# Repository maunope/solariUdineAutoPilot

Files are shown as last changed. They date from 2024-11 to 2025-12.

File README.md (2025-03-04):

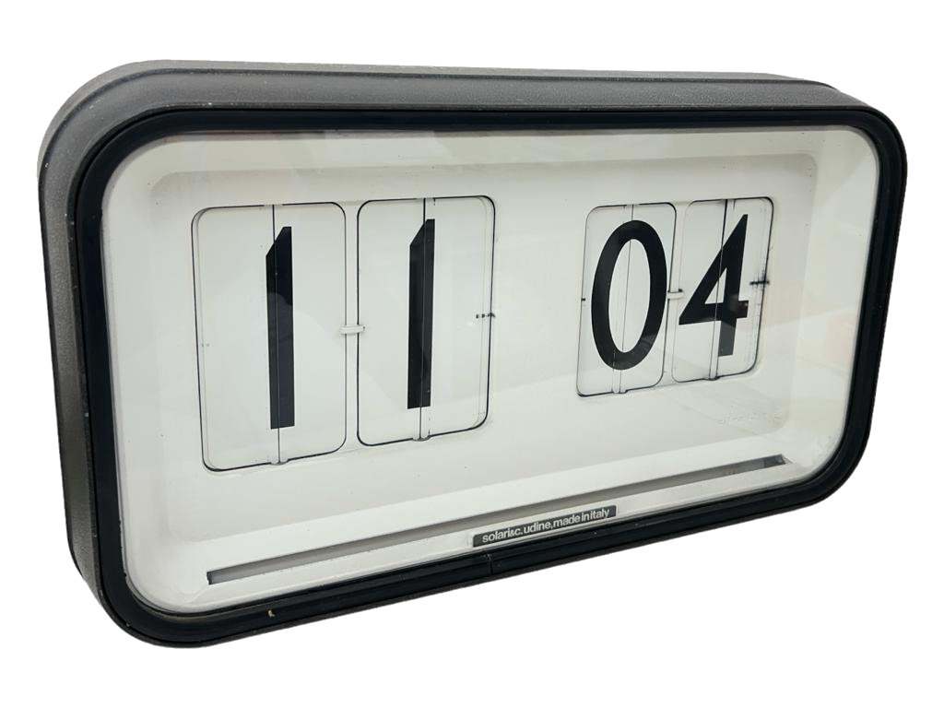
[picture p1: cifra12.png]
Solari Udine Cifra 12


# Disclaimer
This is still a prototype, the circuit design was built and tested on a perfboard, the kicad board design was never tested.  use at your risk and plz **don't  come whining if you damage your flip clock or set your house on fire.**

# Solari Udine Auto Pilot

Arduino based Solari Udine Clock controller, suitable for alternating pulse Solari Udine Clock motors (i.e. Cifra 12). Controls hours and minutes, no calendar functions are provided. The current board design accepts a single Vcc in, either 12V or 24V, from an external power source. 

**Main features:**   
- Self adjusts after a power loss
- Handles DST (Central Europe rules)
- Allows manual adjustment

A led provides visual feedback, an optional LCD1602 can be plugged in to display status.

The software tries to mitigate strain on the flip clock limiting the number and frequency of rollers turns:
- Turns are limited to 1 every 3 seconds (manual step adjustment bypasses this)
- If the clock is more than 120 minutes behind, movement is paused till the next day (a halted clock displays the right time once a day after all **:-)**)
- If the eeprom or rtc module fail, no pulses are sent to the motor
- If the rtc module crashes, attempts are made to restore the last known consistent timestamp
- A hardware circuit limits pulse duration and frequency to 1 second.
- the circuit board has hardware protection avoiding prolonged motor pulses, set to 1 second. Once a pulse is sent, following ones are delayed until the hw protection has completed its cycle. Note that it is totally possible to build the board without the 555 timer, just hardwire L293D enable pins to high, software will work just fine.

The following features improve durability and operation:
- The system self restart once per week
- Eeprom writes are spread over a 256kbit eeprom, this should guarantee at least 20 years of operation before writes start to fail, more likely 50-70
- If eeprom stored time is unavailable, the clock halts until it is adjusted
- If RTC module is unavailable, the clock blinks for 30 seconds and then resets
- The Arduino will stay powered down approx 95% of the time during regular operation, saving considerable power. As a side effect, minutes will flip within +/- 2 seconds of when RTC time ticks a minute.  

## Dependencies

- [LiquidCrustal I2C](https://github.com/johnrickman/LiquidCrystal_I2C)
- [RTClib](https://github.com/adafruit/RTClib)
- [Regexp](https://github.com/nickgammon/Regexp)
- [SparkFun External EEPROM Arduino Library](https://github.com/sparkfun/SparkFun_External_EEPROM_Arduino_Library)
- [Rocket Scream Low Power](https://github.com/rocketscream/Low-Power)

## Circuit Board

**WORK IN PROGRESS** check the schematic in this repo, I've built and tested it on perfboard, board design might not be 100% correct, and definitely the layout could 
use some improvement.

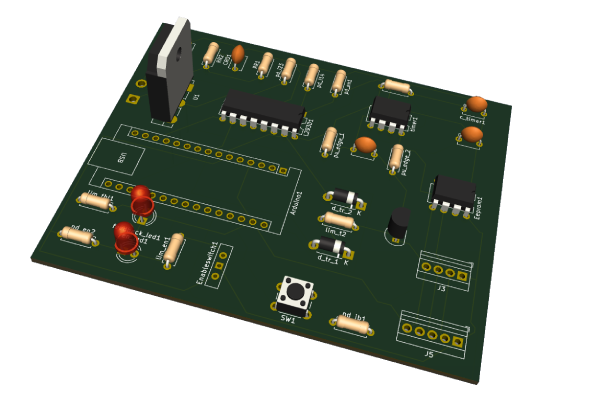
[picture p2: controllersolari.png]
Solari Udine Autopilot Circuit Board


**"Simplified"** board version uses some 30% less components removing the following features:

- Hardware limitation of pulses duration
- Paralleled L293D outputs

Considering how unlikely it is for the sketch to remain stuck with motor output set high, you might want to save yourself some hassle, expecially if you're building on perfboard.

I've built the board using these cheap DS3231 bought off Amazon, the design uses a male connector matching their Vcc-signal-signal-NC-Ground pinout, you might want to use something different and change the board design accordingly.
One good thing about these is they're small enough and can be easily swapped for testing and debugging

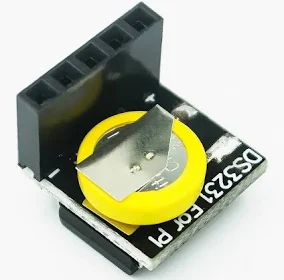
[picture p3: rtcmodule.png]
RTC Module


**How to read led signals**

Either for good or bad news, green led will flash. red will stay on when general enable switch is on

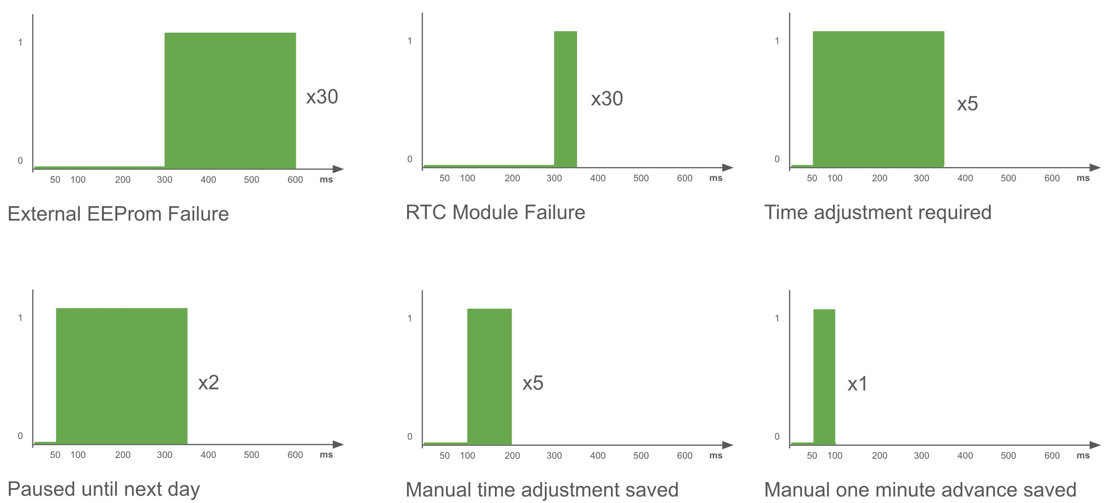
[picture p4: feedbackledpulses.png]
Feedback led pulses interpretation card


## How to install and adjust

**First things first, let's not fry stuff**
- If you built the board yourself, either run the Arduino sketch with  SET_COMPILE_TIME_TO_RTC flag turned on or use serial commands to prime the RTC module.
- Check your clock coil working voltage. Most accept 24V plus 12V or 48V with different wiring. **The current board design was tested with a 12 V external power source, 24V should work fine albeit with the tension regulator running hotter, 48V is beyond the regulator specs**
- Check your coil max current draw, one L293D with paralleled channels can drive up to 1200mA, no Solari Udine clock should draw more than that
- Unplug the clock, wire your power supply and the clock motor coil
- Turn the enable switch *OFF*
- Power the board.
 **No smoke? good.**
- On the first start, a manual time adjust is required,  "Time Adjustment Required" pattern will flash on the feedback led
- Manually adjust the clock flip rolls to match current time, the optional LCD display displays it on the first line
- Dial at least one minute advance with the button, this will prime pulse direction
- When the clock time matches RTC time, *Press the push button for 3 seconds until "Manual Time Adjustment Saved" pattern flashes*
- Turn the enable switch *ON*

The controller will now keep the flip clock display aligned with the internal RTC clock.

## Enabling motor movement

A switch allows to pause motor movement for maintenance and dialing in commands, the clock will catch up automatically once enable is resumed.
A led will remain **ON** while movement is paused.
the switch also disables deep sleep time and prepares the Arduino for accepting commands: wait until feedback led blinks once after pausing movement, then dial button or serial commands.

## Push buttons commands

*Important* only dial pushbutton commands with the motor enable switch turned off 

- Brief press: advances the clock 1 minute, led blinks briefly
- Three seconds press: aligns eeprom time with RTC time, for manual adjustment, led blinks on a pattern 

## Serial port commands

*Important* only dial serial commands with the motor enable switch turned off 

Commands format: **(<<|>>)[A-Z]{1,10}[a-z,A-Z,0-9]{1,20}**

- **<<** to read info, **>>** to set
- command name, in caps
- (where applicable) parameter

One command per line, max 32 chars long. the parser is pretty crude, pls stick to tested commands ;-) 

**Available commands**:

- **<<BOOTTIMESTAMP** prints the curent boot timestamp
- **>>COMPILEDATETIME** align RTC date and time to the sketch compilation timestamp
- **<<COMPILEDATETIME** print the sketch build timestamp
- **>>DAILYSECODNSOFFSET[+-][0-9]{3}$** (i.e: >>DAILYSECODNSOFFSET+010, DAILYSECODNSOFFSET+000, DAILYSECODNSOFFSET-020) stores the desided number of daily RTC error compensation to eeprom.
- **<<DAILYSECODNSOFFSET** print daily seconds of  RTC error correction setting stored in the eeprom
- **>>RTCDATETIMEyyymmddhhmmss** (i.e: >>DATETTIME20241119235959) set RTC date and time, takes standard time, *not DST*.
- **<<RTCDATETIME** print RTC date and time
- **<<EEPROMDATA** print eeprom date, time and clock status information

## Build flags

-DEBUG_MODE enable serial port and LCD debug messages, disbales sleep time  and force reinitialization of eeprom and rtc module on each read
-SET_COMPILE_TIME_TO_RTC forces writing sketch build time to RTC on each boot, only use to program new rtc modules.

## Troubleshooting
**Q:** Instead of catching up the clock is standing still and the "Paused until next day" pattern flashes:

**A:** When more than 120 minutes are to be catched up, automatic adjustment will pause and wait for clock time to be right again the next day.

**Q:** The Arduino keeps resetting every half a minute or so, the feedback led flashes

**A:**  Either the eeprom or RTC clock aren't responding, the board needs fixing

**Q:**  I've hooked up a display, now what?

**A:** Note that the display only works when DEBUG_MODE flag is raised

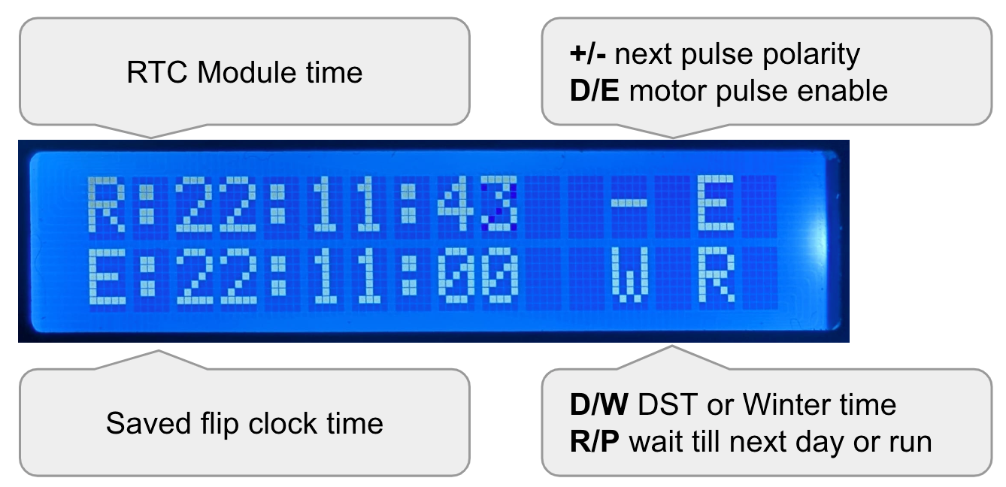
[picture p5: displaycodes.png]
Optional display fields


**Q:**  How can I tell if my eeprom is corrupted or simply requires initialization?

**A:**  "Adj. time" on the display or "No valid time set in eeprom, please adjust clock" on the Serial are good news.

**Q:** My RTC module lost its time configuration!

**A:** >>DATETIME[0-9]+ command should fix it, however, if it happens again, the module batttery might be drained

**Q:** I can't tell what's going on with eeprom data

**A:** <<EEPROMDATA command can extracts all the info saved on the eeprom

**Q:** LCD doesn't display anyting, and/or serial messages are missing

**A:** set DEBUG_MODE build flag and upload firmware again

**Q:** **(serial|button) commands** are not working!

**A:** they only work reliably when motor movement is paused (solid red led), during regular operation the Arduino is awake and responding to commands for only few seconds per minute, good luck catching it awake! :-) 

**Q:** My clock drifts X seconds ahead/behind everyday

**A:** Buy a proper RTC module next time! :-) there's a handy feature to correct this, if the drift is the same every day, see serial commands

**Q:** My clock drifts X *minutes* ahead/behind everyday

**A:** Hikes! that's not OK! try a different RTC module, then check your board for errors on I2C bus pullup resistors and +5v power. I've tested the board design powering I2C devices straight from a tension regulator bypassing the Arduino's internal one, either do the same or dig  sleep configurations to figure how to keep the RTC powered during sleep. In case you figure something out, open a PR here :-)

**Q:** I got a RTC failure message/blink and then the board rebooted

**A:** Your RTC went nuts! it happens every now and then with cheap *ss modules, mine's MBTF is around 4 months, the sketch tries its best to recover to the last timestamp that made sense if it detects the RTC is acting up

**Q:** No matter what I do, the clock keeps flipping!

**A:** The RTC module is returning wrong timestamps, and the checks I've put in place are not working. :-( 
    compile the sketch in debug mode, use serial commands to check what timestamp is recorded in the RTC module and fix it, 
    realing eeprom time with RTC time, reboot, and check after a few minutes that the RTC module is behaving. If you wish, drop me an email about the problem including the timestamp you had in the RTC module and then one in you EEPROM (or, even better, figure what's wrong and open a PR :-) )

**Q:** That PCB design is **lame**!

**A:** It is. any help much appreciated! ;-)

## Todo
- when disabling motion while sleep is skipped (i.e. 2 secs after a pulse), feedback led doens't blink
- Add support for bluetooth communication
- Improve kicad design
- Figure some predictable behavior for when RTC is known to be f*cked up, i.e start from 1970 and stop calculating dst
- Finish String calss removal
- Remove dependency from regexp library

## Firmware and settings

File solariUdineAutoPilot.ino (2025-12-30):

//#define DEBUG_MODE

#ifdef DEBUG_MODE
#include <LiquidCrystal_I2C.h>         //https://github.com/johnrickman/LiquidCrystal_I2C
#endif

#include <LowPower.h>                  //https://github.com/rocketscream/Low-Power
#include <RTClib.h>                    //https://github.com/adafruit/RTClib
#include <SparkFun_External_EEPROM.h>  //https://github.com/sparkfun/SparkFun_External_EEPROM_Arduino_Library



//never leave this flag on on regular operation, it pretty much defeats the purpose of using this board
//#define SET_COMPILE_TIME_TO_RTC

//struct for the EEProm index page
struct EepromIndexDescriptor {
  unsigned long signature;
  int pageOffset = 0;
  int dailySecondsOffset = 0;
};

// struct for clock status to be saved to the eeprom
struct EepromData {
  //initializing at WINT_MAX ensures that if the conrtoller is run without further initialization
  //it won't send pulses
  DateTime dateTime = DateTime(WINT_MAX);
  int nextPulsePolarity = 0;
  int currentWrites = 0;
  bool pausedTillNextDay = false;
};


//debug mode redirects stdout to the serial port, this avoids the need for strings buffering
#ifdef DEBUG_MODE
// Define a custom putchar function to redirect output to Serial
int putCharToSerial(char c, FILE *stream) {
  if (stream == stdout) { // Check if it's standard output
    Serial.write(c);
  }
  return 0;
}

// Declare a FILE stream for stdout (no initializer here!)
FILE customStdOut;
//printf macro, together with putCharToSerial driver debug messages straight to the Serial port,
//stores string in Program Memory and appends a new line to each log line automatically
#define DEBUG_PRINTF(format, ...) printf_P(PSTR(format "\n"),##__VA_ARGS__);
#endif

#ifndef DEBUG_MODE
#define DEBUG_PRINTF(format, ...) // Nothing 
#endif






const unsigned long EEPROM_SIGNATURE = 0xD24F789F;
const int EEPROM_PAGE_SIZE_BYTES = 64;
const int MAX_WRITE_PER_EEPROM_PAGE = 10080;  // approx one week of regular operation
const int EEPROM_SIZE_BYTES = 32768;
const int EEPROM_TYPE = 256;
const int EEPROM_ADDRESS_BYTES = 2;
// to avoid straining the clock, if time is more than 120 seconds off will
// remain still until the next day
const int MAX_CATCHUP_MINUTES = 120;
const int SEC_IN_MINUTE = 60;
const int NO_SLEEP_AFT_COMM_SECS = 10;
const int PUSH_BUTTON_PIN = 0;
const int MOTOR_PULSE_ENABLE_PIN = 6;
const int MOTOR_PULSE_UP_PIN = 7;
const int MOTOR_PULSE_DOW_PIN = 8;
const int FEEDBACK_LED_PIN = 9;
const int WAIT_NEXT_PULSE_CYCLE_PIN = 10;
// duration of motor pulses, note shorter between circuit 555 timer and this
// applies
const int PULSE_DURATION_MILLIS = 400;
// minimun delay between pulses, overridden by manual advances. real Solari
// Udine controllers use 4s
const int SECS_BETWEEN_PULSES = 3;

//if the RTC module went ahead more than these seconds since last time it was read, then we can assume it went nuts
//max difference should be 5s
const int RTC_FUBAR_SECONDS = 30;

DateTime bootTime = DateTime((unsigned long)0);
DateTime lastCommandReceived = DateTime((unsigned long)0);
// when true the clock will not self adjust until  RTC times is one full day
// ahead, then eeprom time will be bumped 24hrs, within MAX_CATCHUP_MINUTES, and
// self adjustment will take place
bool pausedTillNextDay = false;
// tracks last pulse sent to motor, to enforce max pace set by SECS_BETWEEN_PULSES
DateTime lastPulseTime = DateTime((uint32_t)0);
// these two are true when a pulse was delayed to way until the hardware pulse
// time protection has cycled
bool bookedPulseManual = false;
bool bookedPulseAuto = false;
// how long the push button has been pressed
unsigned long pushButtonPressedMillis = 0;
DateTime lastDailyOffsetCorrection = DateTime((uint32_t)0);


//Optional LCD Display
#ifdef DEBUG_MODE
LiquidCrystal_I2C lcd(0x27, 16, 2);
#endif

//Real Time Clock Module
RTC_DS3231 rtc;
//External eeprom to save current clock status
ExternalEEPROM extEeprom;



DateTime previousRTCDateTime = DateTime((unsigned long)0);

//sets DS3231 settings, crappy Ds3231 chips are finicky about power cuts and sometimes get their
//settings corrupted, so we reset them to a known good state each time we boot
void setDS3231Defaults() {
  // Set Control Register to default low power mode
  // DS3231_OFF sets INTCN=1, and disables SQW generation
  rtc.writeSqwPinMode(DS3231_OFF);

  // Disable Alarms (clears A1IE and A2IE bits in Control Register)
  rtc.disableAlarm(1);
  rtc.disableAlarm(2);

  // Clear Alarm Flags (clears A1F and A2F bits in Status Register)
  rtc.clearAlarm(1);
  rtc.clearAlarm(2);

  // Disable 32kHz output (clears EN32kHz bit in Status Register)
  rtc.disable32K();
  DEBUG_PRINTF("DS3231 defaults available through RTC lib set");
  // Explicitly clear EOSC (Bit 7) to ensure oscillator runs on battery
  // and clear BBSQW (Bit 6) to disable square wave on battery (low power).
  // RTClib doesn't expose direct access to these bits for DS3231.
  Wire.beginTransmission(0x68); // DS3231 I2C address
  Wire.write(0x0E);             // Control Register
  Wire.endTransmission();
  Wire.requestFrom(0x68, 1);
  if (Wire.available()) {
    uint8_t ctrl = Wire.read();
    ctrl &= ~0xC0; // Clear Bit 7 (EOSC) and Bit 6 (BBSQW)
    Wire.beginTransmission(0x68);
    Wire.write(0x0E);
    Wire.write(ctrl);
    Wire.endTransmission();
    DEBUG_PRINTF("DS3231 defaults set");
  }
  else
  {
     DEBUG_PRINTF("Failes to set DS3231 defaults");
  }
}

void setup() {

  // Init pins
  pinMode(MOTOR_PULSE_ENABLE_PIN, INPUT);
  pinMode(MOTOR_PULSE_UP_PIN, OUTPUT);
  pinMode(MOTOR_PULSE_DOW_PIN, OUTPUT);
  pinMode(FEEDBACK_LED_PIN, OUTPUT);
  pinMode(PUSH_BUTTON_PIN, INPUT);
  pinMode(WAIT_NEXT_PULSE_CYCLE_PIN, INPUT);
  digitalWrite(MOTOR_PULSE_UP_PIN, LOW);
  digitalWrite(MOTOR_PULSE_DOW_PIN, LOW);
  digitalWrite(FEEDBACK_LED_PIN, LOW);

  // Init Serial and i2c modules
  Serial.begin(19200);

#ifdef DEBUG_MODE
  //if in debug mode, redirect stdout to serial
  fdev_setup_stream(&customStdOut, putCharToSerial, NULL, _FDEV_SETUP_WRITE);
  stdout = &customStdOut; // Redirect stdout to our stream
#endif

  Wire.begin();
  Wire.setClock(400000);
  extEeprom.setMemoryType(EEPROM_TYPE);
  extEeprom.setMemorySizeBytes(EEPROM_SIZE_BYTES);
  extEeprom.setAddressBytes(EEPROM_ADDRESS_BYTES);  // Set address bytes and page size after  MemorySizeBytes()
  extEeprom.setPageSizeBytes(EEPROM_PAGE_SIZE_BYTES);


  // check if the eeprom is available and initialize its parameters, check for
  // valid time in the eeprom is repeated in the loop
  if (!extEeprom.begin()) {
    DEBUG_PRINTF("External eeprom Error");
    blinkFeedbackLed(300, 300, 30);
    // reset
    asm volatile("  jmp 0");
  }


  /*EepromData blankTimeData;
     blankTimeData.dateTime = WINT_MAX;
     blankTimeData.nextPulsePolarity = 0;
     blankTimeData.currentWrites = 0;

     writeTimeDataToEeprom(blankTimeData);*/

  // Under no circumnstance read/write the RTC module when not ready!
  // if RTC is unavailabe sends a blink pattern and then resets
  if (!rtc.begin()) {
    DEBUG_PRINTF("RTC Error");
    blinkFeedbackLed(50, 300, 30);
    // reset
    asm volatile("  jmp 0");
  }
  setDS3231Defaults();
  previousRTCDateTime = getRTCDateTime();



#ifdef SET_COMPILE_TIME_TO_RTC
  rtc.adjust(getStandardTime(DateTime(F(__DATE__), F(__TIME__))));
#endif

#ifdef DEBUG_MODE
  lcd.init();
  lcd.backlight();
  lcd.clear();
#endif

  //update boot time if it's not set
  if (bootTime == DateTime((unsigned long)0)) {
    bootTime = getRTCDateTime();
  }
  lastDailyOffsetCorrection = bootTime;

}



// blinks the feedback led alternating given on/off time, for the given number
// of times. restores initial state after blinking
void blinkFeedbackLed(int onMillis, int offMillis, int iterations) {
  int initialState = digitalRead(FEEDBACK_LED_PIN);
  for (int i = 0; i < iterations; i++) {
    digitalWrite(FEEDBACK_LED_PIN, HIGH);
    delay(onMillis);
    digitalWrite(FEEDBACK_LED_PIN, LOW);
    delay(offMillis);
  }
  digitalWrite(FEEDBACK_LED_PIN, initialState);
}



// writes EepromData struct to the eeprom, spreading writes over pages to
// maximize the eeprom life. if the eeprom has no record of the current page, a
// new index page is created and writes restart from the first available page
int writeTimeDataToEeprom(EepromData& eepromData) {
  const int eepromDataPagesSizeBytes = ceil(sizeof(EepromData) / (float)EEPROM_PAGE_SIZE_BYTES) * EEPROM_PAGE_SIZE_BYTES;
  const int eepromIndexDescriptorSizeBytes = ceil(sizeof(EepromIndexDescriptor) / (float)EEPROM_PAGE_SIZE_BYTES) * EEPROM_PAGE_SIZE_BYTES;
  EepromIndexDescriptor eepromIndexDescriptor;
  eepromIndexDescriptor.signature = 0;

  // check if first 4 bytes contain the required signature string
  extEeprom.get(0, eepromIndexDescriptor);


  // check if first 4 bytes contain the required signature string

  if (eepromIndexDescriptor.signature != EEPROM_SIGNATURE) {
    // EEPROM is not initialized, write the signature and default address and
    // set 0 writes in counter

    DEBUG_PRINTF("EEprom not initialized, setting index page");
    eepromIndexDescriptor.signature = EEPROM_SIGNATURE;
    // set to the number of bytes containing the descriptor
    eepromIndexDescriptor.pageOffset = eepromIndexDescriptorSizeBytes;

    extEeprom.put(0, eepromIndexDescriptor);

    // write a blank time, setting to WINT_MAX ensures this dummy time will
    // prevent unwanted pulses
    EepromData blankTimeData;
    blankTimeData.dateTime = WINT_MAX;
    blankTimeData.nextPulsePolarity = 0;
    blankTimeData.currentWrites = 0;
    extEeprom.put(eepromIndexDescriptor.pageOffset, eepromIndexDescriptor);
  }

  EepromData currentEepromData;
  extEeprom.get(eepromIndexDescriptor.pageOffset, currentEepromData);

  // switch to next page if the number of writes on the current one exceeds the
  // desided value
  if (currentEepromData.currentWrites > MAX_WRITE_PER_EEPROM_PAGE) {
    // switch forward one page, if
    // we reached the top, start back from first page after index
    eepromIndexDescriptor.pageOffset =
      (eepromIndexDescriptor.pageOffset + eepromDataPagesSizeBytes < EEPROM_SIZE_BYTES)
      ? eepromIndexDescriptor.pageOffset + eepromDataPagesSizeBytes
      : eepromIndexDescriptorSizeBytes;
    eepromIndexDescriptor.signature = EEPROM_SIGNATURE;
    extEeprom.put(0, eepromIndexDescriptor);
    // reset writes counter in currentEepromData
    eepromData.currentWrites = 0;
  } else {
    // write to eeprom and track we have +1 write on the current page
    eepromData.currentWrites = eepromData.currentWrites + 1;
  }

  extEeprom.put(eepromIndexDescriptor.pageOffset, eepromData);

  return 1;
}

// Function to read data from EEPROM, returns -1 and sets dateTime to WINT_MAX
// if the eeprom is uninitialized setting dateTime to WINT_MAX is a safety
// measure: it avoids any random/unwanted impulse as RTC time will always be
// lower
int readEepromData(EepromData& eepromData) {
  EepromIndexDescriptor eepromIndexDescriptor;
  extEeprom.get(0, eepromIndexDescriptor);

  // check if first 4 bytes contain the required signature string
  if (eepromIndexDescriptor.signature != EEPROM_SIGNATURE) {
    //todo check if this works
    DEBUG_PRINTF("EEprom is not initialized: got %lX instead of %lX ", eepromIndexDescriptor.signature, EEPROM_SIGNATURE);
    // EEPROM is not initialized, return 0
    eepromData.dateTime = WINT_MAX;
    eepromData.nextPulsePolarity = 0;
    return -1;  // Indicate that EEPROM is not initialized
  }

  extEeprom.get(eepromIndexDescriptor.pageOffset, eepromData);
  return 1;  // Data read successfully
}

//reads daily seconds offset from eeprom, returns 0 if can't read
int getDailySecondsOffsetFromEeprom() {
  const int eepromIndexDescriptorSizeBytes = ceil(sizeof(EepromIndexDescriptor) / (float)EEPROM_PAGE_SIZE_BYTES) * EEPROM_PAGE_SIZE_BYTES;

  EepromIndexDescriptor eepromIndexDescriptor;
  // check if first 4 bytes contain the required signature string
  extEeprom.get(0, eepromIndexDescriptor);


  if (eepromIndexDescriptor.signature != EEPROM_SIGNATURE) {
    // EEPROM is not initialized, write the signature and default address and
    // set 0 writes in counter
    DEBUG_PRINTF("getDailySecondsOffsetFromEeprom, EEprom not initialized, call writeEepromData first");
    return 0;
  }
  return eepromIndexDescriptor.dailySecondsOffset;
}

// writes dailySecondsOffset in the eeprom, returns -1 if can't write
int writeDailySecondsOffsetToEeprom(int dailySecondsOffset) {
  const int eepromIndexDescriptorSizeBytes = ceil(sizeof(EepromIndexDescriptor) / (float)EEPROM_PAGE_SIZE_BYTES) * EEPROM_PAGE_SIZE_BYTES;

  EepromIndexDescriptor eepromIndexDescriptor;
  eepromIndexDescriptor.signature = 0;

  // check if first 4 bytes contain the required signature string
  extEeprom.get(0, eepromIndexDescriptor);


  if (eepromIndexDescriptor.signature != EEPROM_SIGNATURE) {
    // EEPROM is not initialized, write the signature and default address and
    // set 0 writes in counter
    DEBUG_PRINTF("writeDailySecondsOffsetToEpprom, EEprom not initialized, call writeEepromData first");
    return -1;
  }
  eepromIndexDescriptor.dailySecondsOffset = dailySecondsOffset;


  extEeprom.put(0, eepromIndexDescriptor);
  return 1;
}
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
void loop() {



  if (Serial.available() > 0) {
    char command[128];
    int i = 0;
    while (Serial.available() > 0 && i < 127) {
      char c = Serial.read();
      if (c == '\n') {
        break;  // Break when newline character is received
      }
      command[i] = c;
      i++;
    }
    command[i] = '\0';
    parseSerialCommands(command);
  }


  bool motorPulseEnable = digitalRead(MOTOR_PULSE_ENABLE_PIN) == HIGH;

  // RTCDateTime is the time coming from the battery backed Real Time Clock
  // module, always in standard time
  DateTime RTCDateTime = getRTCDateTime();


  //sometimes cheap *ss RTC modules go nuts,
  //this simple check restores the last assumed valid RTC time in case what comes from the module is obviously off
  //I'm not compensating the time spent looping since last update, which should be <5seconds anyway
  //I'm making the assumption the RTC timestamp was good at boot.
  //the remote risk of RTC fucking up right after boot or while the board is powered off is left unchecked, worst that will happen is
  //the board will drive the clock to a wrong timestamp, which users will notice pretty easily
#ifndef DEBUG_MODE
  if ((RTCDateTime > previousRTCDateTime && (RTCDateTime - previousRTCDateTime).totalseconds() > RTC_FUBAR_SECONDS) || RTCDateTime < previousRTCDateTime ) {
    Serial.println(F("RTC Module went nuts! restoring last assumed good time and reebooting"));
    rtc.adjust(previousRTCDateTime);
    blinkFeedbackLed(50, 300, 30); //rtc failure led blink
    asm volatile("  jmp 0");
  }
#endif
  previousRTCDateTime = RTCDateTime;


  // DST adjusted version of RTCDateTime
  DateTime dstAdjRTCDateTime = getDSTAdjustedTime(RTCDateTime);

  //once every 24hours, apply seconds offset to compensate RTC drift
  //24hrs are counted since boot, considering power outages are expected to be rare, it's worth drifting a few seconds
  //every now and then to spare eeprom writes, in case of a long power outage, a manual time set is advisable anyway
  if ((RTCDateTime - lastDailyOffsetCorrection).totalseconds() >= SECONDS_PER_DAY)
  {
    int dailySecondsOffset = getDailySecondsOffsetFromEeprom();
    if (dailySecondsOffset != 0) {
      RTCDateTime = RTCDateTime + TimeSpan(dailySecondsOffset);
      rtc.adjust(RTCDateTime);
      DEBUG_PRINTF("Applied daily seconds offset: %d", dailySecondsOffset);
    }
    lastDailyOffsetCorrection = RTCDateTime;
  }

  // self reset every week+5minutes, just in case I f*cked up and some variable would
  // overflow left unchecked.
  //Serial.println(String((RTCDateTime-bootTime).totalseconds())+" "+String(SECONDS_PER_DAY*7));
  if ((RTCDateTime - bootTime).totalseconds() >= (SECONDS_PER_DAY * 7) + 300) {
    asm volatile("  jmp 0");
  }



  // EEPromTimeData is the last recorded time, polarity and no of writes on the
  // current eeprom page  that was pulsed to the moto
  EepromData eepromData;
  readEepromData(eepromData);
  // if EEprom has no valid time set, skip clock movement and notify user
  if (!eepromData.dateTime.isValid()) {
#ifdef DEBUG_MODE
    lcd.setCursor(0, 0);
    lcd.print("Adj. time");
#endif
    DEBUG_PRINTF("No valid time set in eeprom, please perform manual adjustment");

    blinkFeedbackLed(300, 50, 5);
  } else {

    // regular operation

    // if the motor enable signal is turned off, don't calculate/send pulses
    if (motorPulseEnable) {
      // if the clock has been sleping for days, skip them until it's <24hours
      // behind, only hh:mm matters anyway
      while ((dstAdjRTCDateTime - eepromData.dateTime).days() > 0) {
        // not saving this to eeprom on purpose, no flip movement, in case of a
        // power loss this calculation will be performed again
        eepromData.dateTime = eepromData.dateTime + TimeSpan(SECONDS_PER_DAY);
      }

      // less than 24hrs, possible situations:
      //  - clock is less than MAX_CATCHUP_MINUTES behind -> regular catch up,
      //  following  code section will take care of it
      //  - clock is more than MAX_CATCHUP_MINUTES -> wait until it's e more
      //  than 24hrs behind again, then the while cycle a few lines above will
      //  bump it within the MAX_CATCHUP_MINUTES interval (note that bumping
      //  24hrs immediately would give the same result )

      // if actual time is more than one minute ahead of what has been already
      // pulsed to the motor, shoot one pulse pace pulses every
      // SECS_BETWEEN_PULSES seconds to avoid straining the flip clock

      // bookedPulse means a pulse (manual or automatd) has to be dealyed
      // because hardware protection cycle hadn't finished ther

      long rtcEepromTimeDiffSeconds = (dstAdjRTCDateTime - eepromData.dateTime).totalseconds();
      //Serial.println(RTCDateTime.timestamp()+" "+lastPulseTime.timestamp());
      if (((rtcEepromTimeDiffSeconds > SEC_IN_MINUTE) && ((RTCDateTime - lastPulseTime).totalseconds() > SECS_BETWEEN_PULSES)) || bookedPulseAuto) {
        DEBUG_PRINTF("rtcEepromTimeDiffSeconds: %ld bookedPulseAuto: %d", rtcEepromTimeDiffSeconds, bookedPulseAuto);
        //check if we need to wait till tomorrow
        if ((rtcEepromTimeDiffSeconds / SEC_IN_MINUTE >= MAX_CATCHUP_MINUTES) && !bookedPulseAuto) {
          if (eepromData.pausedTillNextDay == false) {
            eepromData.pausedTillNextDay = true;
            writeTimeDataToEeprom(eepromData);
          }
          blinkFeedbackLed(300, 50, 2);
        } else {
          // shoot a pulse
          if (digitalRead(WAIT_NEXT_PULSE_CYCLE_PIN) == LOW) {
            sendPulse(eepromData, PULSE_DURATION_MILLIS);
            // record the last pulsed time, advance by one minute
            eepromData.dateTime = eepromData.dateTime + TimeSpan(SEC_IN_MINUTE);
            eepromData.pausedTillNextDay = false;
            writeTimeDataToEeprom(eepromData);
            lastPulseTime = RTCDateTime;
            bookedPulseAuto = false;
          } else {
            DEBUG_PRINTF("Delaying synchronization pulse");
            bookedPulseAuto = true;
          }
        }
      }
    }
    pulseDebugStringToDisplay(eepromData, dstAdjRTCDateTime, motorPulseEnable, isDST(RTCDateTime));
  }
  // handle inputs from pushbutton
  // brief press: advance flip clock by one minute
  // 3 seconds press: align EEPromTime to RTCDateTime, to be used after manual
  // flip clock adjustment
  if (digitalRead(PUSH_BUTTON_PIN) == HIGH) {

    lastCommandReceived = RTCDateTime;
    if (pushButtonPressedMillis == 0) {
      pushButtonPressedMillis = millis();
    }
    // long press
    else if (millis() - pushButtonPressedMillis >= 3000) {
      // this totals to 1 second
      blinkFeedbackLed(100, 100, 5);
      // sets the current Secs on the eeprom to the value coming from the RTC,
      // setting seconds to zero
      eepromData.dateTime = dstAdjRTCDateTime - TimeSpan(dstAdjRTCDateTime.second());
      eepromData.pausedTillNextDay = false;
      writeTimeDataToEeprom(eepromData);
      //this helps when debugging, clock will start self adjustig immediately
      lastPulseTime = RTCDateTime;
      DEBUG_PRINTF("Manual Adjustment completed");
      delay(200);  //avoid bounces
      pushButtonPressedMillis = 0;
    }
  }
  // short press
  else if (pushButtonPressedMillis > 0 || bookedPulseManual) {
    DEBUG_PRINTF("Manual pulse requested");
    pushButtonPressedMillis = 0;
    if (digitalRead(WAIT_NEXT_PULSE_CYCLE_PIN) == LOW) {
      blinkFeedbackLed(100, 0, 1);
      sendPulse(eepromData, PULSE_DURATION_MILLIS);
      eepromData.dateTime = eepromData.dateTime + TimeSpan(SEC_IN_MINUTE);
      writeTimeDataToEeprom(eepromData);
      DEBUG_PRINTF("Sent a manual pulse %s" , (bookedPulseManual ? "booked" : ""));
      bookedPulseManual = false;
    } else {
      DEBUG_PRINTF("Delaying manual pulse");
      bookedPulseManual = true;
    }
  }


  //go to sleep in low power mode fo deepSleepSeconds
  //doesn't sleeep for 20 seconds after a button press
  //doesn't sleep if there's a delayed pulse to send out
  //doesn't sleep for 2x pulse delay after a pulse was sent
  //won't sleep if motorPulseEnable is off, this helps debugging :-)
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

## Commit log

2024-11-11 snapshot circuito
2024-11-13 added external i2c eeprom usage
2024-11-13 updated circuit image
2024-11-15 added multi day catch up, corected flaw on RTC initialization during DST, minor bugs
    [solariUdineAutoPilot.ino]
2024-11-17 updated board
2024-11-17 added kicad first version
    [Arduino Autopilot.kicad_pcb, Arduino Autopilot.kicad_sch]
2024-11-18 updated board circuit, added serial commands parsing, update documentation
    [Arduino Autopilot.kicad_pcb, Arduino Autopilot.kicad_sch]
2024-11-22 fixed dst management when sending manual inputs, fixed delay capacitor wiring in circuit
    [Arduino Autopilot.kicad_pcb, Arduino Autopilot.kicad_sch]
2024-11-24 updated pin layout, updated circuit and board design
    [Arduino Autopilot.kicad_pcb, Arduino Autopilot.kicad_sch]
2024-11-24 update circuit
    [Arduino Autopilot.kicad_sch]
2024-11-25 added simplified kicad design
    [Aurduino Autopilot Kicad - Simplified.kicad_pcb, Aurduino Autopilot Kicad - Simplified.kicad_sch]
2024-11-28 fixed sleep mode, updated diagrams
    [Arduino Autopilot.kicad_pcb, Arduino Autopilot.kicad_sch, Aurduino Autopilot Kicad - Simplified.kicad_pcb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]
2024-11-28 fixed hanging wire
    [Aurduino Autopilot Kicad - Simplified.kicad_pcb]
2024-11-28 added drift correction, update circuit and doc
    [Aurduino Autopilot Kicad - Simplified.kicad_sch]
2025-02-22 - added RTC module failure check - added deug_printf mode - (WIP) removing string class usage
    [solariUdineAutoPilot.ino]
2025-02-28 fixed sprintf, mad liquidcrystal optional
    [solariUdineAutoPilot.ino]
2025-03-04 fixed debug mode printf
    [solariUdineAutoPilot.ino]
2025-03-04 Fixed serial strings, fixed readme
    [solariUdineAutoPilot.ino]
2025-07-10 fixed a but on long button press com mand bug that halted the clock for 1h when long button press command was issued during DST period
    [solariUdineAutoPilot.ino]
